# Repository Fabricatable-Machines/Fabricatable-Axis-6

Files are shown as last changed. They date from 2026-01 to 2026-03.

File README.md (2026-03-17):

# Fabricatable-Axis-6
A low cost linear actuator for digital fabrication machines. Open hardware designed in open software. Easy to 3D print parts with an easy to source BOM.

Developement of this project is supported by patreons of Jens Dyvik and the UK Risa fund through Adam Smith International.

*Status: Under development, the first protypes are assembled but not properly tested*

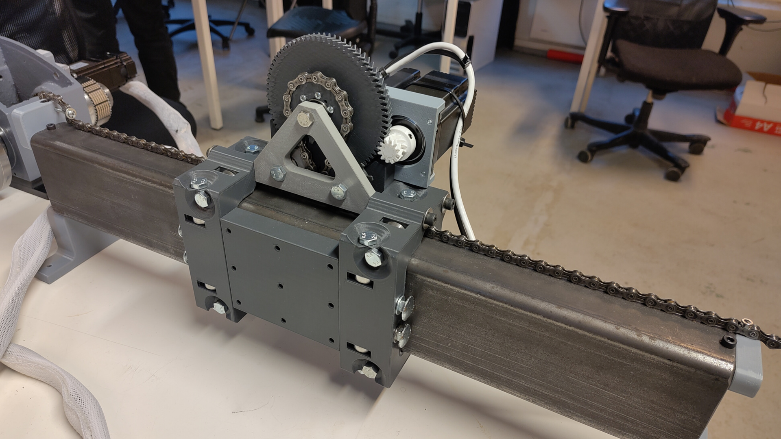
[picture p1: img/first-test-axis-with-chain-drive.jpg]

*First prototype with a bicyccle chain drive and 608 bearings*

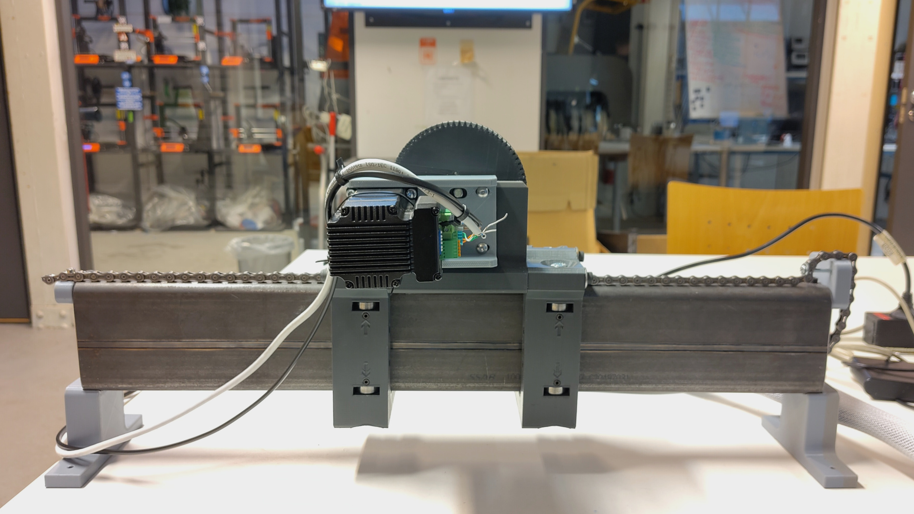
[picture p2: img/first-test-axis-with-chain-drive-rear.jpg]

*Rear view of the first prototype*

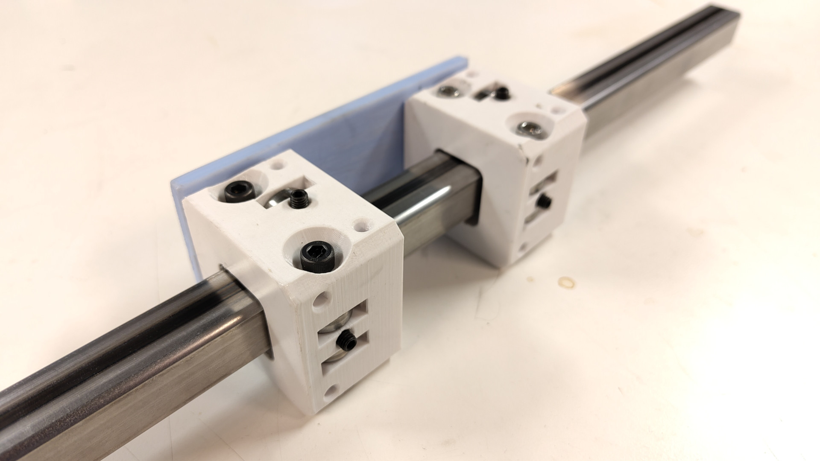
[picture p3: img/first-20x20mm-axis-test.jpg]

*A first test for smaller axis with 625 bearings running on a 20mm x 20mm steel tube*

### BOM

**For two bearing rings - Large** *Two sets of bearing rings needed for one axis*
- 608 2RS bearing (with rubber seal on both sides)- 12pcs
- M8 screw - 40mm length (any scew head type works) - 12pcs - *to function as axles for the bearings*
- M5 set screw - preferably 10mm length (any normal M5 screw 16mm length or more will also work, but will protrude) - 6pcs - *for fine tuning bearing pressure*

**Additional hardware for the belt drive version**
- M5 hex socket head 1-16mm length - 4pcs - *to attach the nema23 stepper*
- GT2 timing gear pulley - 8mm bore - for 9mm wide belts - 20 teeth - 1pcs - *to drive the belt*
- GT2 timing belt 9-10mm wide - with fiber arming - 1pcs - *to position the carriage on the axis*

**Additional hardware for the bicycly drive version**
- Standard 1/2 inch link length bicycle chain - 1pcs *adjust paremteres in the FreeCAD file to compensate for chain waear*
- 608 2RS bearing (with rubber seal on both sides) - 4pcs
- M8 screw - 40mm length (any scew head type works) - 2pcs
- M8 screw - 80mm length - 1pcs
- Short M3 screws - unknown amount
- A few M8 washers - Unknown amount
- M5 set screw - preferably 10mm length - *for locking the pinion on the motor shaft*
- Short M5 screws - 8pcs - *for attaching the motor to the motor platean dthe motor plate to the carriage*
- 70mm or longer M6 screws - 4pcs - *for attahcing the bearings rings to the chain drive*

**For one bearing ring - Samll** *Two sets of bearing rings needed for one axis*
- 625 2RS bearing (with rubber seal on both sides)- 12pcs
- M5 screw - 20mm length (any scew head type works) - 12pcs - *to function as axles for the bearings*
- M3 set screw - 5-10mm lengt (any normal M3 screw 16mm length or more will also work, but will protrude) - 6pcs - *for fine tuning bearing pressure*

### 3D printing parts

- All parts are desgined to be 3D printed with no support
- Reccomended material: PETG
- Reccomended shells/walls: 4-6
- Reccomeded top/bottom layers: 4-6
- Infill is not so important, default 20% will work fine
- Default 0.4mm dimater nozels work fine. But a 0.6mm or 0.8mm is faster and makes stronger prints

### Assembly

- All screws self tap, no tapping needed
- More info coming later

### Tuning

- Use the set screws to fine tune the pressure of the bearings on the steel tube
-More info coming later

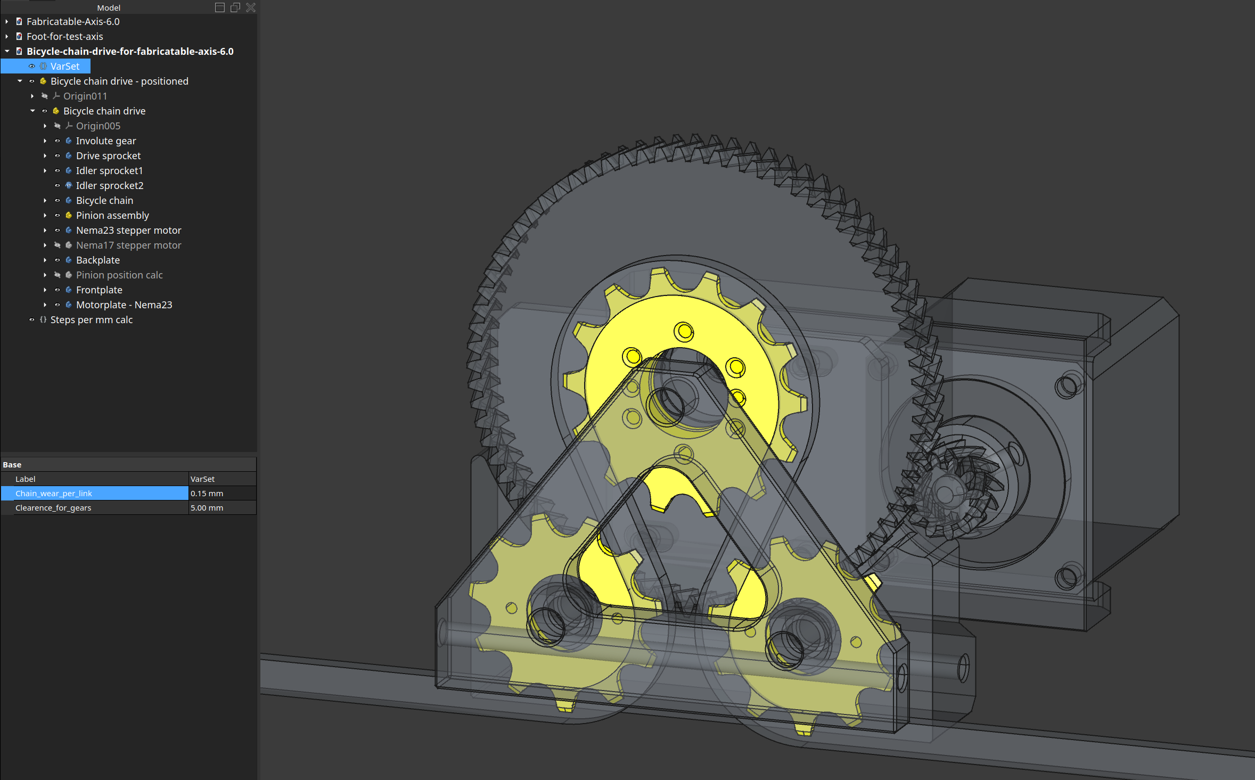
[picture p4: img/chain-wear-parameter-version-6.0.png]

*It is possible to adjust a paramter to compensate for chin wear when using second hand bicycle chains. Adjust the paramter, print a sprocket, check the fit, and repaeat untill the chain wraps around the sprocket without popping or shifting.*

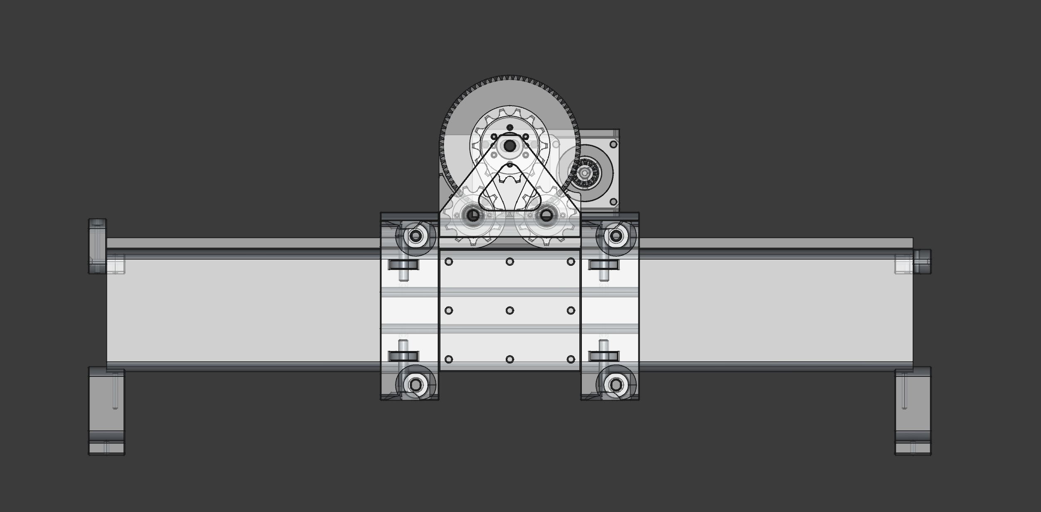
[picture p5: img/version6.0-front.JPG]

*Front view of the first bicycle chain drive*

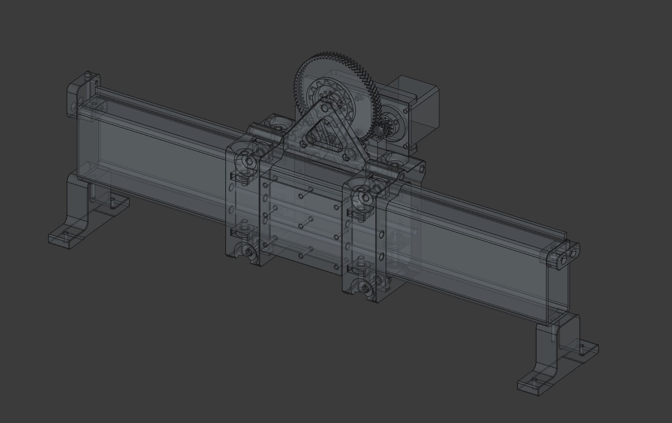
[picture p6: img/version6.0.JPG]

*Perspective view of the first bicycle chain drive*

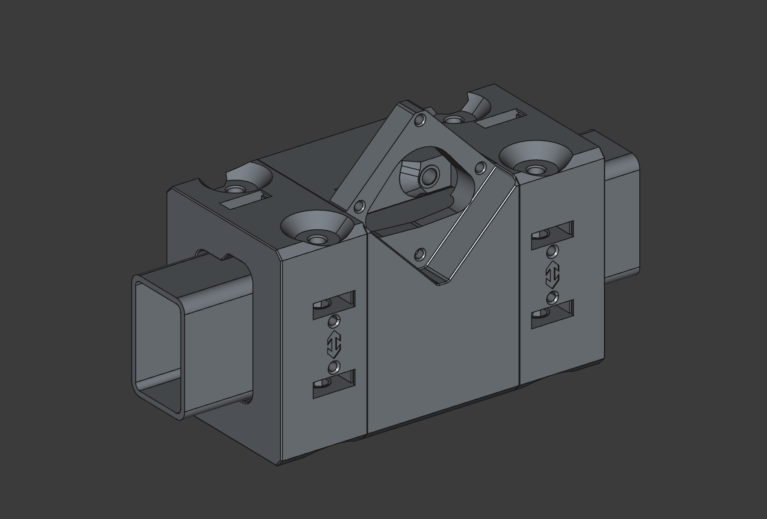
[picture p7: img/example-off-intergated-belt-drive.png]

*Example of an integrated for a single 3D print - two bearings rings and a belt drive in one part*

License: Creative Commons Attribution-ShareAlike 4.0

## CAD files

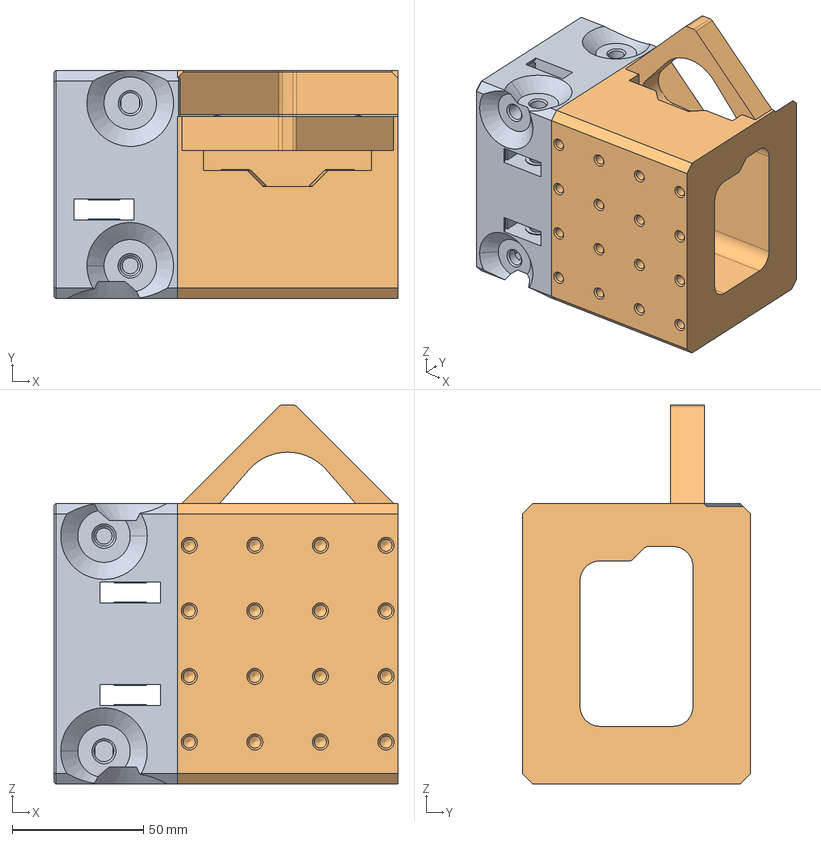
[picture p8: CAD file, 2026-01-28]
Version6.01/60mmx40mm-tube-version/FreeCAD/Fabricatable-Axis-6.01-60mmx40mm-tube-version-Belt-drive-assembly.FCStd
131.0 x 87.0 x 144.5 mm
Bearing ring - with all booleans (Mirror #1)
Connecting body

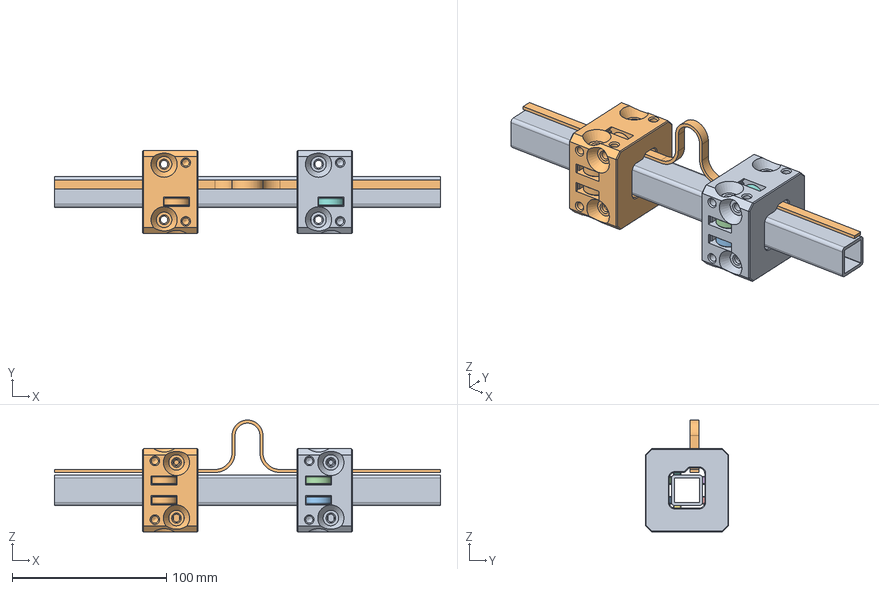
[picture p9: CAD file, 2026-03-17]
Version6.01/20mmx20mm-tube-version/FreeCAD/Fabricatable-Axis-6.01-20mmx20mm-tube-version-Bearing-ring.FCStd
250.0 x 54.0 x 72.5 mm
Steel tube
Belt
Bearing001
Bearing002
Bearing003
Bearing004
Bearing005
Bearing006
Bearing ring - with chamfers and booleans
Bearing ring 2

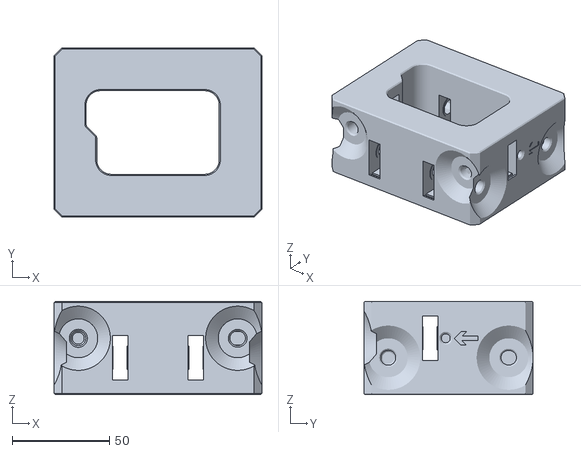
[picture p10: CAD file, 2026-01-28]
Version6.01/60mmx40mm-tube-version/Stl/Fabricatable-Axis-6.01-60mmx40mm-tube-version-Bearing-ring-no-attachment-hoels.stl
107.0 x 87.0 x 48.0

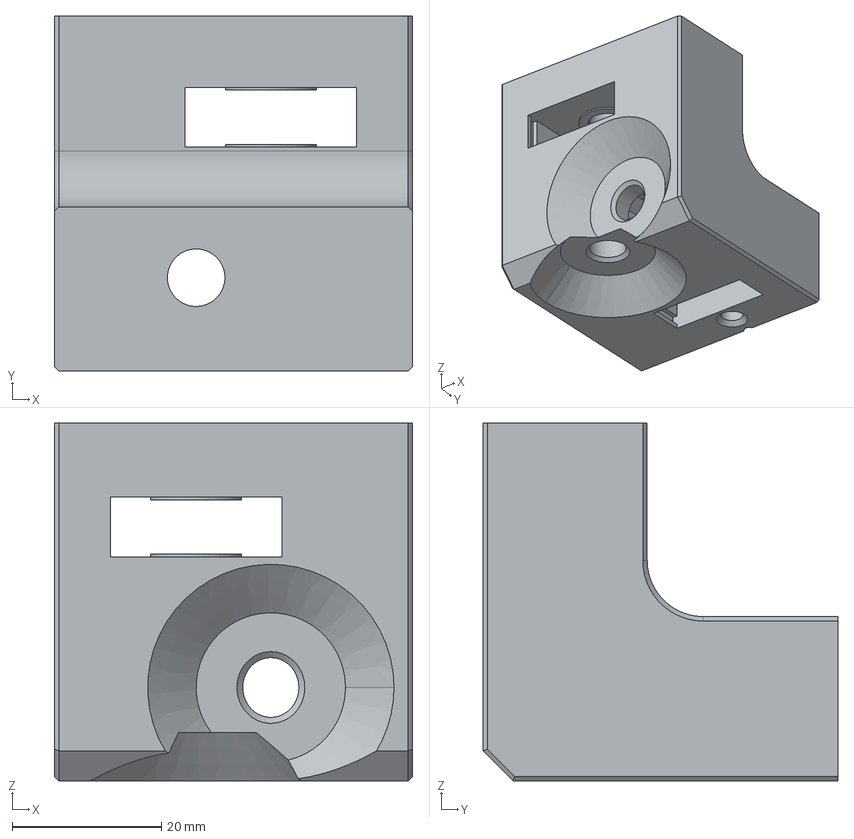
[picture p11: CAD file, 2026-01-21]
Version6.01/Testpiece/Step/Testpiece_from_60mmx40mm_tube_version.step
48.0 x 47.5 x 47.9 mm

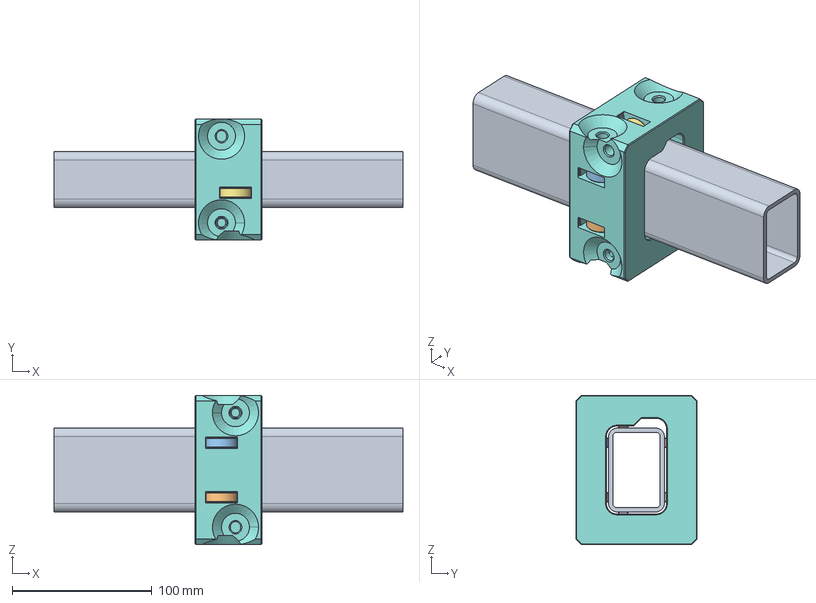
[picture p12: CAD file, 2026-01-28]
Version6.01/60mmx40mm-tube-version/FreeCAD/Fabricatable-Axis-6.01-60mmx40mm-tube-version-Bearing-ring.FCStd
250.0 x 87.0 x 107.0 mm
Steel tube
Bearing001
Bearing002
Bearing003
Bearing004
Bearing005
Bearing006
Bearing ring - with all booleans

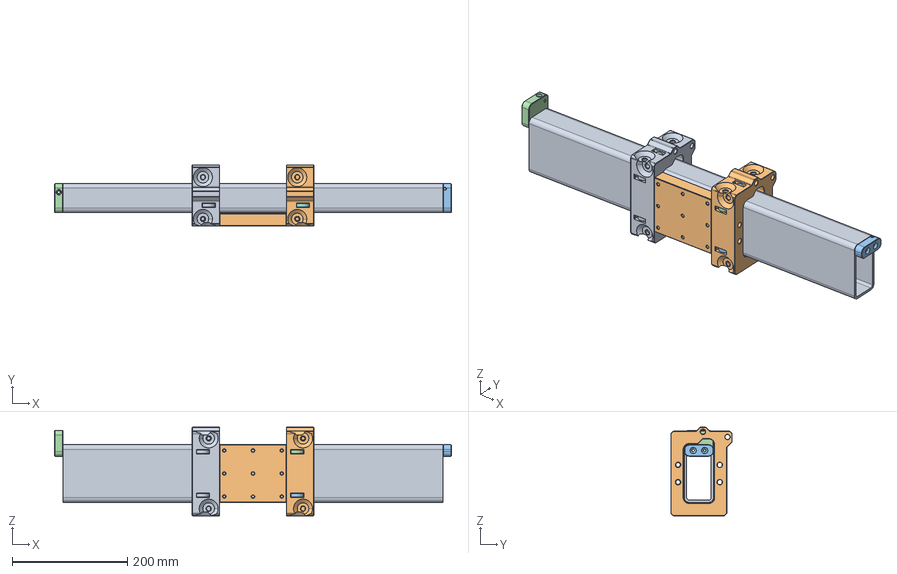
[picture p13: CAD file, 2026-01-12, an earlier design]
Version6.00/FreeCAD/Fabricatable-Axis-6.0.FCStd
690.0 x 106.5 x 154.0 mm
Steel tube
Carriage body - with holes cut
Bearing001
Bearing002
Bearing003
Bearing004
Bearing005
Bearing006
Bearing ring 2
Connector for bearing rings
Chain lock - non-adjustable
Chain lock - adjustable

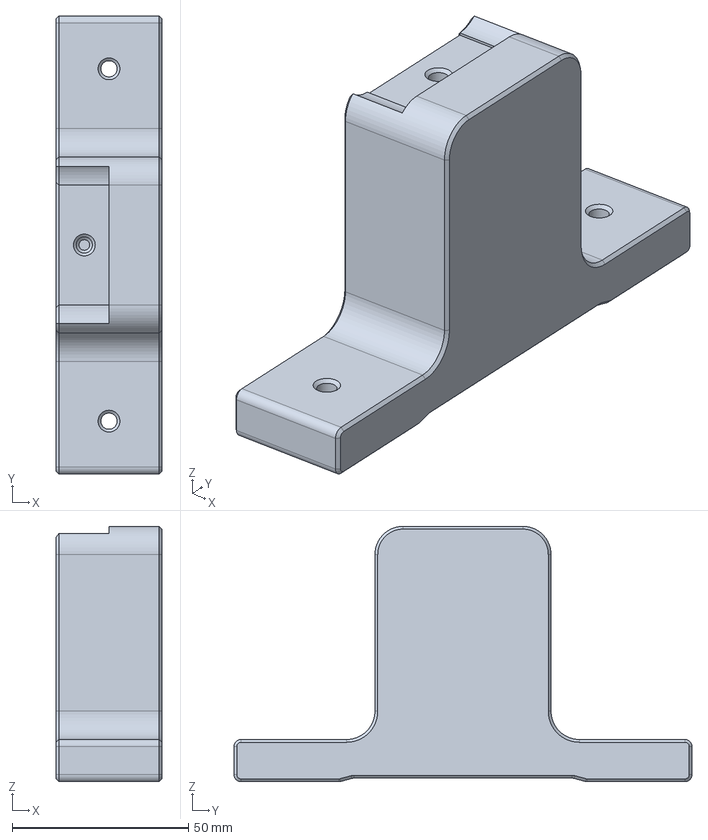
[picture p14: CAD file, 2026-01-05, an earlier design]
Version6.00/FreeCAD/Foot-for-test-axis.FCStd
30.0 x 130.0 x 72.5 mm

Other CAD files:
Version6.01/Testpiece/FreeCAD/Testpiece_from_60mmx40mm_tube_version.FCStd
Version6.01/Testpiece/Step/Stl/Testpiece_from_60mmx40mm_tube_version.stl
Version6.01/Testpiece/Stl/Testpiece_from_60mmx40mm_tube_version.stl

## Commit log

2026-01-05 Added linked parts
    [Fabricatable-Axis-6.0.FCStd, Foot-for-test-axis.FCStd]
2026-01-12 Added image
    [Fabricatable-Axis-6.0.FCStd]
2026-01-21 Added testpiece from version 6.01
    [Fabricatable-Axis-6.0.FCStd, Foot-for-test-axis.FCStd, Testpiece_from _60mmx40mm_tube_version-Testpiece.step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]
2026-01-21 Fixed name typo
    [Testpiece_from _60mmx40mm_tube_version-Testpiece.step, Testpiece_from_60mmx40mm_tube_version.FCStd, Testpiece_from_60mmx40mm_tube_version.step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]
2026-01-21 added support button
2026-01-21 Work on belt drive assembly
    [Fabricatable-Axis-6.01-60mmx40mm-tube-version-Bearing-ring.FCStd, Fabricatable-Axis-6.01-60mmx40mm-tube-version-Belt-drive-assembly.FCStd, Testpiece_from_60mmx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]
2026-01-22 added missing stl
    [Testpiece_from_60mmx40mm_tube_version.stl]
2026-01-28 Completed first spiral of bel tdrive assembly
    [Fabricatable-Axis-6.01-60mmx40mm-tube-version-Bearing-ring.FCStd, Fabricatable-Axis-6.01-60mmx40mm-tube-version-Belt-drive-assembly.FCStd]
2026-01-28 Added stl of single bearing ring
    [Fabricatable-Axis-6.01-60mmx40mm-tube-version-Bearing-ring-no-attachment-hoels.stl]
2026-01-28 fixed print orientation
    [Fabricatable-Axis-6.01-60mmx40mm-tube-version-Bearing-ring-no-attachment-hoels.stl]
2026-03-17 added belt drive screenshot
2026-03-17 started work on BOM
2026-03-17 added first 20x20mm version
    [Fabricatable-Axis-6.01-20mmx20mm-tube-version-Bearing-ring-with-attachment-holes.stl, Fabricatable-Axis-6.01-20mmx20mm-tube-version-Bearing-ring.FCStd]
2026-03-17 added stls from first proptype
    [Bicycle chain drive sketch-Bicycle chain drive - positionedSimple pinion - with 8mm bore.stl, Bicycle chain drive sketch-Bicycle chain driveDrive sprocket.stl,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]
2026-03-17 added chain wear parameter screenshot
2026-03-17 Update README with 3D printing and assembly details
    Added sections on 3D printing parts, assembly, and tuning.
